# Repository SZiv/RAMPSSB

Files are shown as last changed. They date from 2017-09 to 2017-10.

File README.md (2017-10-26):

# RAMPSSB
=== Be sure to take a look at the Wiki before attempting a build: http://reprap.org/wiki/RAMPSSB and if you are curious more as to the development and technological reasoning behind this project, take a look at my blog post at http://scottziv.com/rampssb-bringing-closed-loop-dc-motor-control-to-3d-printers/ ===

RAMPS Servo Board. Released under GPLv3.

Replaces the X and Y stepper drivers on a RAMPS CNC control board with two channel DC motor quadrature encoder control using cheap, common, easy to solder components. Compatable with almost any 0-24V DC motor with a quadrature encoder that uses hall effect, optical, or mechanical rotary encoders. 

Uses a square L298N DC motor driver, attached with standoffs to the PCB, over 2 Arduino Pro Micros for control. PCB board is less than 100m square, so it can be produced for $5 + shipping from Seeedstudio, and the L298N driver board is cheap (like $3), and the controllers, Pro Micros, are maybe 5 bucks a piece.

For more steppers, this is compatable with the Reprap.me stepper expander, or, with some modification, my other board, the RAMPSXB. 

Can also be used as a simple non-RAMPS step/direction to DC encoder motor setup by directly wiring the pins. 

The firmware could use some work, and I am slowly developing it. It does function, but it is not as stable as I would like. If anyone has better luck with control software, let me know and I can add it to the official repo.

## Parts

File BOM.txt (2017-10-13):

1x PCB
1x L298N DC motor driver (the square kind)
2x Arduino Pro Micro (NOT PRO MINI! Sparkfun makes these, but there are plenty of clones) 
1x filtering capacitor for the motor power if you think its nessissary.
a bunch of male and female pin headers
3x M3x20mm spacers w/screws and nuts
1x M3x5 screws with nuts
1x 3D printed "RAMPSSBSingleFanMount.stl"
1x 40mm fan

If you are dealing with a lot of power, the drivers are stackable, and two pins are included for each control pin, so you dont need to splice wires for two drivers. However, you can theoretically stack these as high as you want and run them in parallel. Drivers can handle about 2 amps per channel.
1x L298N DC motor driver (the square kind)

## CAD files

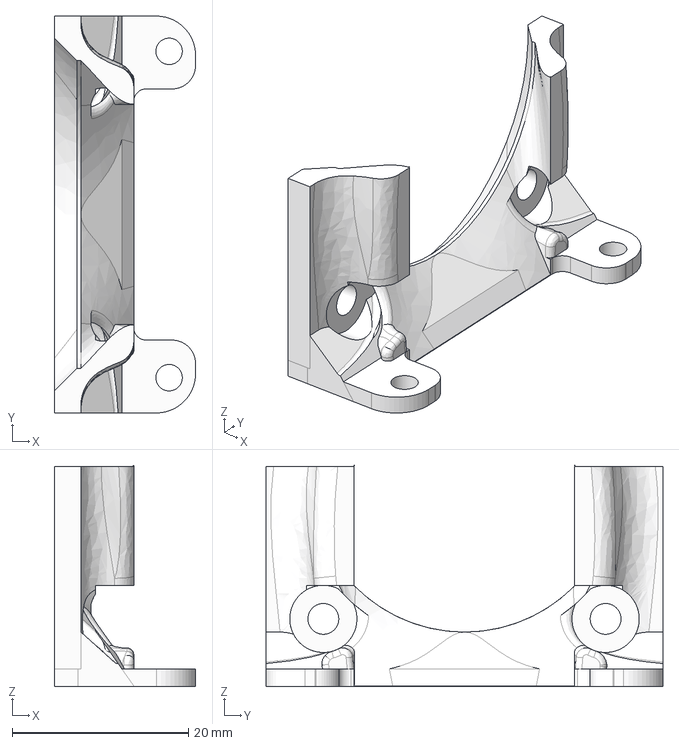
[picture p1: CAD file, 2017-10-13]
Models/RAMPSSBSingleFanMount.step
16.0 x 45.0 x 25.1 mm

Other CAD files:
Models/RAMPSSBSingleFanMount.stl

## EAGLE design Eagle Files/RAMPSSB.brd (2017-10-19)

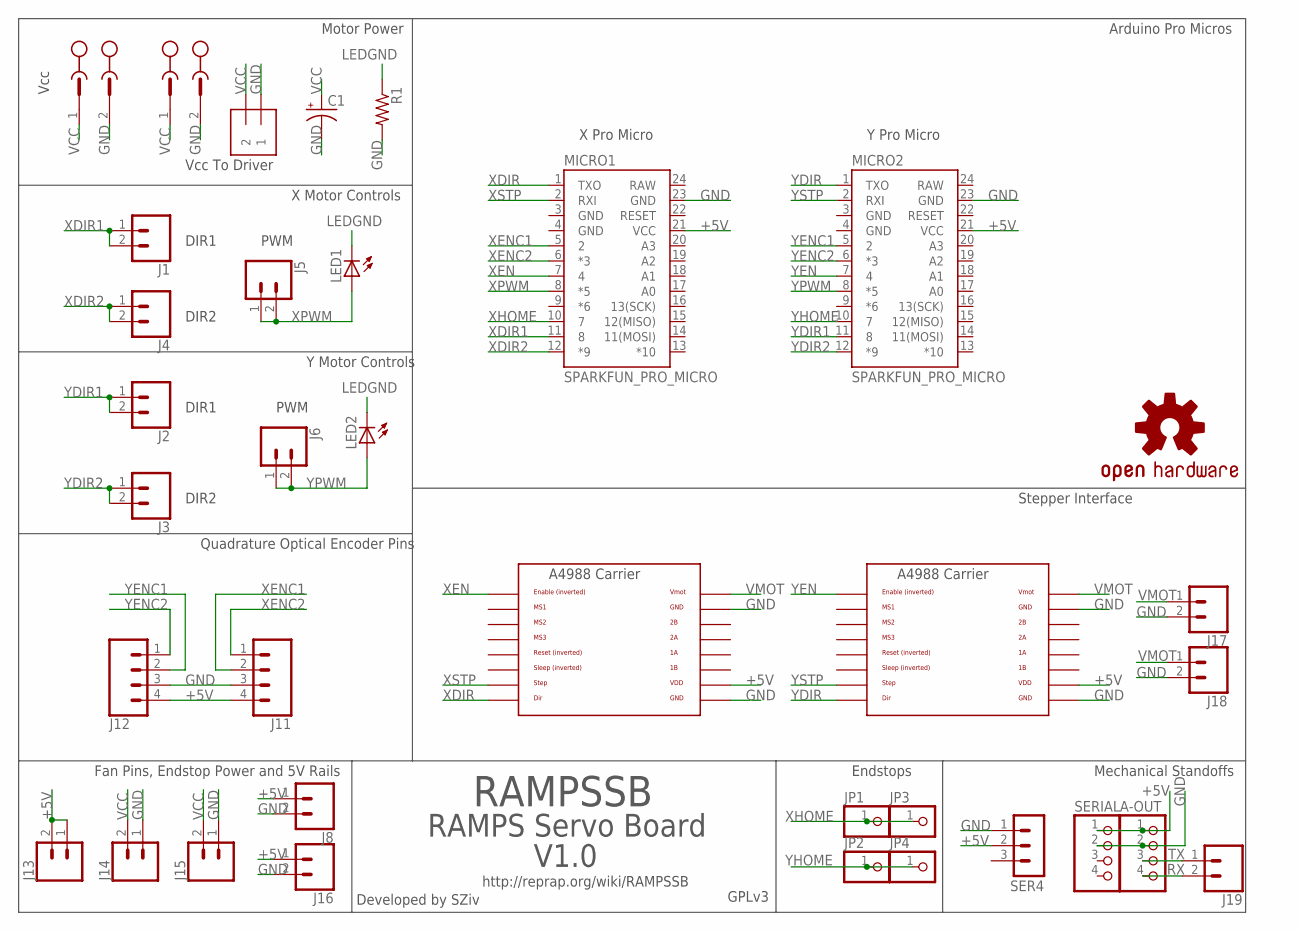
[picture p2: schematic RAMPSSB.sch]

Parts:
A-OUT: PINHD-1X4; 1X04
C1: CPOL-USE2.5-6; E2,5-6
J1, J2, J3, J4, J5, J6, J8, J13, J14, J15, J16, J17, J18, J19: CONN_02; 1X02
J7, J9: OSTTH020160; EDSTL130-02
J10: 1X2-3.5MM
J11, J12: CONN_04; 1X04
JP1, JP2, JP3, JP4: PINHD-1X1; 1X01
LED1, LED2: LED3MM
LOGO1: OSHW-LOGOL; OSHW-LOGO-L
MICRO1, MICRO2: SPARKFUN_PRO_MICRO
R1: R-US_0207/7; 0207/7
SER4: 3PIN-HEADER
SERIAL: PINHD-1X4; 1X04
U$6, U$7: A4988BREAKOUT

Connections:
+5V: A-OUT.1, J8.1, J11.4, J12.4, J13.1, J13.2, J16.1, MICRO1.21 (VCC), MICRO2.21 (VCC), SER4.2, SERIAL.1, U$6.VDD, U$7.VDD
GND: A-OUT.2, C1.-, J7.2, J8.2, J9.2, J10.1, J11.3, J12.3, J14.1, J15.1, J16.2, J17.2, J18.2, MICRO1.3 (GND), MICRO1.4 (GND), MICRO1.23 (GND), MICRO2.3 (GND), MICRO2.4 (GND), MICRO2.23 (GND), R1.2, SER4.1, SERIAL.2, U$6.GND, U$6.GND@0 (GND), U$7.GND, U$7.GND@0 (GND)
LEDGND: LED1.K (C), LED2.K (C), R1.1
RAW: MICRO1.24 (RAW), MICRO2.24 (RAW)
RX: A-OUT.4, J19.2
TX: A-OUT.3, J19.1
VCC: C1.+, J7.1, J9.1, J10.2, J14.2, J15.2
VMOT: J17.1, J18.1, U$6.VMOT, U$7.VMOT
XDIR: MICRO1.1 (TXO), U$6.DIR
XDIR1: J1.1, J1.2, MICRO1.11 (8)
XDIR2: J4.1, J4.2, MICRO1.12 (*9)
XEN: MICRO1.7 (4), U$6.EN
XENC1: J11.2, MICRO1.5 (2)
XENC2: J11.1, MICRO1.6 (*3)
XHOME: JP1.1, JP3.1, MICRO1.10 (7)
XPWM: J5.1, J5.2, LED1.A, MICRO1.8 (*5)
XSTP: MICRO1.2 (RXI), U$6.STEP
YDIR: MICRO2.1 (TXO), U$7.DIR
YDIR1: J2.1, J2.2, MICRO2.11 (8)
YDIR2: J3.1, J3.2, MICRO2.12 (*9)
YEN: MICRO2.7 (4), U$7.EN
YENC1: J12.2, MICRO2.5 (2)
YENC2: J12.1, MICRO2.6 (*3)
YHOME: JP2.1, JP4.1, MICRO2.10 (7)
YPWM: J6.1, J6.2, LED2.A, MICRO2.8 (*5)
YSTP: MICRO2.2 (RXI), U$7.STEP

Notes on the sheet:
DIR1
DIR2
PWM
Vcc To Driver
Vcc
Motor Power
X Motor Controls
Y Motor Controls
Quadrature Optical Encoder Pins
Fan Pins, Endstop Power and 5V Rails
Mechanical Standoffs
Stepper Interface
Arduino Pro Micros
RAMPSSB
RAMPS Servo Board
V1.0
Developed by SZiv
GPLv3
http://reprap.org/wiki/RAMPSSB
Endstops
X Pro Micro
Y Pro Micro

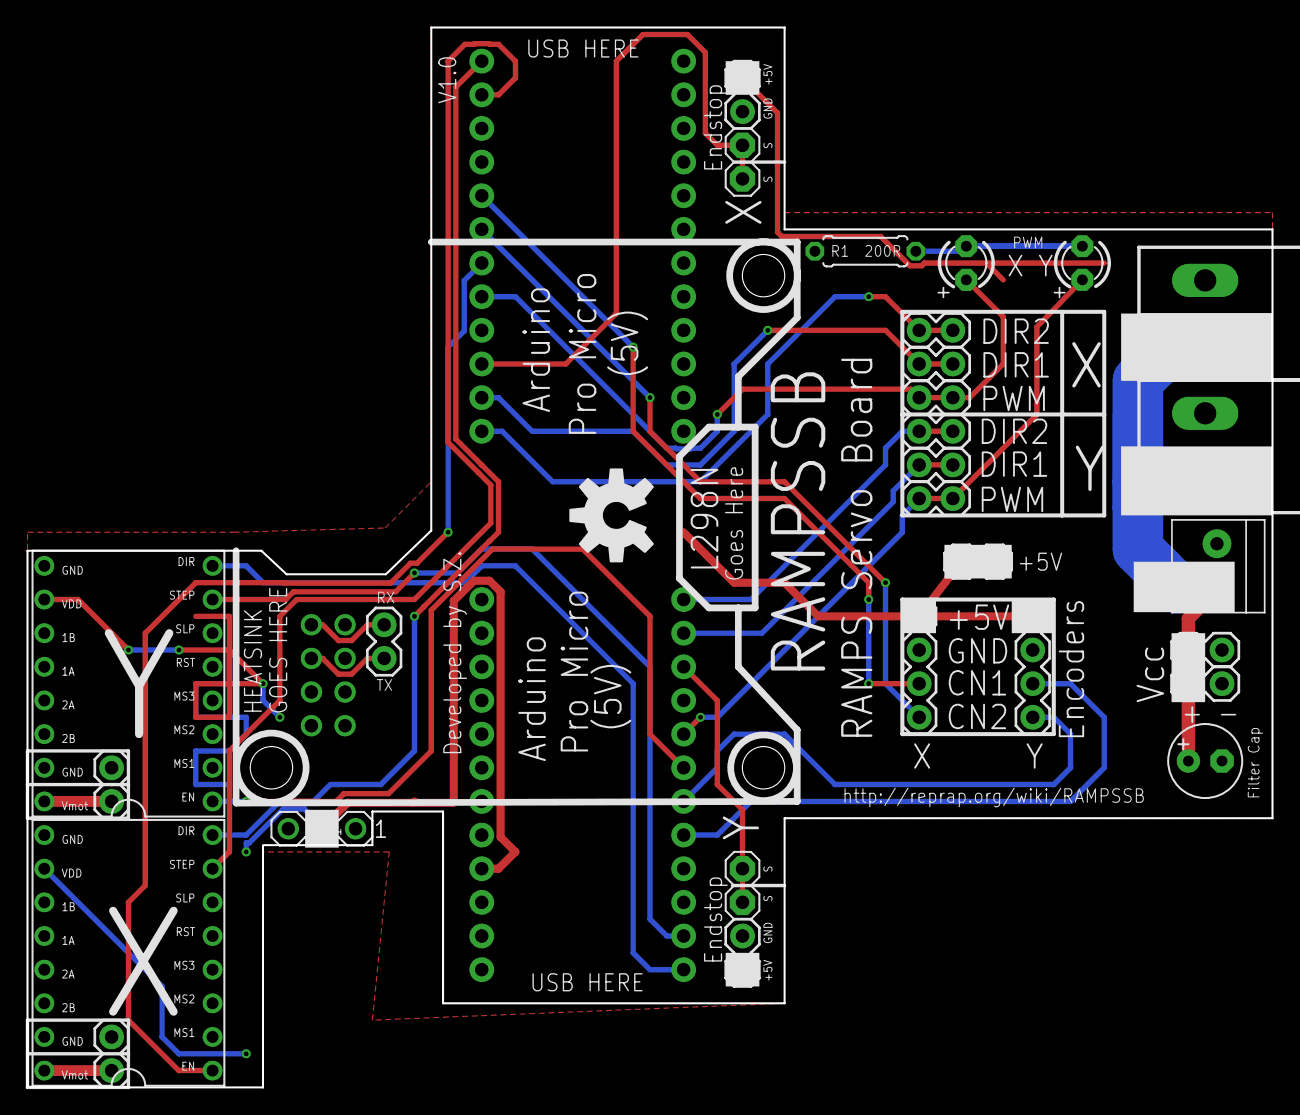
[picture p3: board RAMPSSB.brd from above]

Board: 2 copper layers, 94.0 x 80.0 mm, 35 parts (0 on the bottom side), 26 nets.

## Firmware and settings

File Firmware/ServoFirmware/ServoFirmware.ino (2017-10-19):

#include <Encoder.h> //include encoder library
#include <PID_v1.h> //include PID library
#include "GPIO.h" //include GPIO library

// RAMPSSB Firmware
// Developed by SZiv, released under GPLv3
// Uses PJRC's Encoder library, mikaelpatel's Arduino-GPIO library, as well as Brett Beauregard's PID library. Kudos to them for their hard work!
// Be sure to check out http://reprap.org/wiki/RAMPSSB for more information.

//if you have a better idea of control systems than I, please let me know so I can update the firmware on the official github. It does work, but it has some wobbling error.

//Configuration variables 

//Change these values for your hardware!
#define quadrature true //Is this a quadrature encoder? If so, make true. If you are using a single encoder motor, you will lose a lot of accuracy, but make true (Coming soon!).  
#define cpr 2000.0 //How many counts per revolution? This should be written on the motor datasheet, but its best to test it anyway, because sometimes quadrature encoders have 4 times the noted ticks, because each quadrature counts as 4.
#define mmpr 10 //Millimeters per revolution. This is the DC motor version of "steps per mm" and varies with hardware and gearing. this is easy to test by marking your carriage, rotating the encoder shaft 1 full revolution and measure the distance the carriage moved. 
#define steps_per_mm 80 //What are the steps per mm that the firmware on the RAMPS is using?
#define kp 10 //Proportional Constant. Used for PID control. Tune this to your hardware to get better accuracy. 
#define ki 0 //Integral Constant. Used for PID control. Tune this to your hardware to get better accuracy.
#define kd 1 //Derivative Constant. Used for PID control. Tune this to your hardware to get better accuracy.
#define diagnostic true //If true, sets machine to diagnostic. Prints out location values over serial and can do PID autotuning. Causes a heart attack and bad location data if kept on, so uses it to get PID values and then turn it off.
#define endstopinverted false //By default, endstops are NO. If you are using an NC endstop (like an optical one), change to true.
#define maxpwm 255 //Max PWM you can use on the motor and still read the encoder. For most small encoders that are 100 counts per rev or so, or the speed is low, you can go up to 255, but if you are using faster motors with higher encoder counts, the arduino may freeze up unless you lower this number.  
#define minpwm 110 //Min PWM you can use to make the motor spin.
#define acceptable_error 0.02 //acceptable error for positioning in mm. so long at the carriage is within this value, it will stop. Lowering this value increases accuracy, but my cause wobbling. 

//end of configuration variables



//Define Pins
#define dir 1
#define stp 0
#define en 4
#define pwmout 5
#define encod1 2
#define encod2 3
#define endstop 7
//direction pin setup
GPIO<BOARD::D8> direction1;
GPIO<BOARD::D9> direction2;

//encoder Setup
Encoder myEnc(encod1, encod2); //declare encoder

//PID Setup
double Setpoint = 0;
double Input;
double Output;
PID pidController(&Input, &Output, &Setpoint, kp, ki, kd, DIRECT); //setup PID Controller

//Global Variables
volatile int direct = 0; //What direction are we going? 0 is towards home, 1 is away
//volatile float target = 0; //What is out target location in mm? Updated with new values every step.
//volatile float current = 0; //where are we now? Reset at home
volatile long ticks = 0; //the number of encoder ticks from home we are.
volatile long counts = 0; //number of encoder ticks we are trying to target.
float error = acceptable_error; //acceptable error in mm of final position.
float CPR = cpr; //turn #define into a float
float MMPR = mmpr; //turn #define into a float
float spmm = steps_per_mm; //turn #define into a float
float target = 0;
float current = 0;

void setup()
{
  pinMode(endstop, INPUT);
  pinMode(stp, INPUT);
  pinMode(dir, INPUT);
  pinMode(en, INPUT);
  pinMode(pwmout, OUTPUT);
  direction1.output();
  direction2.output();
  
  //start diagnostic mode
  if (diagnostic == true)
  {
    Serial.begin(250000);
    Serial.println("Diagnostic Mode is Enabled. Turn this off before running the real thing!");
  }

  //set endstop inturrupts
  if (endstopinverted == false)
  {
    attachInterrupt(digitalPinToInterrupt(endstop), reset, RISING); //Reset when the endstop goes from low to high
  }
  else
  {
    attachInterrupt(digitalPinToInterrupt(endstop), reset, FALLING); //Reset when the endstop goes from high to low
  }

  //set encoder inturrupt
  // attachInterrupt(digitalPinToInterrupt(encod1), incretick, RISING); //Add one more step to the total

  //set step inturrupt
  attachInterrupt(digitalPinToInterrupt(stp), increstep, RISING); //Add one more step to the total
  //set DIR inturrupt
  attachInterrupt(digitalPinToInterrupt(dir), directionchange, CHANGE); //flip direction when

  //turn the PID on
  pidController.SetOutputLimits(minpwm, maxpwm); //constrain PID outputs so that it makes the motor run at all levels
  pidController.SetMode(AUTOMATIC);

  //toggle direction
  toggledirection(); //toggle the direction on the DC motor board.
}

void loop()
{
  ticks = myEnc.read(); //update encoder ticks
  target = counts * (1 / spmm); //this is the location in mm we want to be at. (number of steps from home * Steps/mm)
  current = ticks * MMPR * (1 / CPR); //we are currently at this many mm (Encoder ticks from home * mm per revolution / encoder ticks per revolution)
  Input = abs(target - current) * -1; //Input of the PID is negative of the error
  toggledirection(); //check which direction we are going using the direction pin
  pidController.Compute();   //do the PID computation

  if ((digitalRead(en) == 1)||(abs(Input) < error)) //if the motors are disabled or we are within the error of our target, shut motor off
  {
    analogWrite(pwmout, 0); //shut off motors
  }
  else
  {
    analogWrite(pwmout, Output); //output the PID result
  }

  //print location and diagnostic data
  if (diagnostic == true)
  {
    Serial.print("Target:");
    Serial.print(target);
    Serial.print("mm Actual:");
    Serial.print(current);
    Serial.print("mm Steps:");
    Serial.print(counts);
    Serial.print(" Enc_Ticks:");
    Serial.print(ticks);
    Serial.print(" Error:");
    Serial.print(Input);
    Serial.print(" Direction:");
    Serial.print(direct);
    Serial.print(" PWM:");
    Serial.println(Output);
  }
}

void reset()
{
  //reset supposed an actual position
  myEnc.write(0); //reset our encoder position to 0
  counts = 0; //reset out encoder counts to 0

  //Flip direction to make sure we go forward.
  direction1 = LOW;
  direction2 = HIGH;
}

void increstep()
{
  //add or remove a step from the count
  if (direct == 0) //if we are going backwards
  {
    counts--;
  }
  else
  {
    counts++;
  }
}

void incretick()
{
  //add or remove encoder tick from the count
  if (direct == 0)
  {
    ticks--;
  }
  else
  {
    ticks++;
  }
}


void directionchange()
{
  //check direction and tell the motors
  direct = digitalRead(dir);
  toggledirection();
}

void toggledirection()
{
  //make sure the dc motor is moving in the direction we want it to be
  if (current > target)
  {
    direction2 = LOW;
    direction1 = HIGH;
  }
  else if (current < target)
  {
    direction1 = LOW;
    direction2 = HIGH;  
  }
}

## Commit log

2017-09-23 Main Commit
    First Commit. Still waiting on board to test, and I have yet to write
    the software, but its up here if anyone wants to work with it.
    I havent written the Wiki page yet, but once I get a working version,
    I'll throw it up.
    [RAMPSSB.GBL, RAMPSSB.GBO, RAMPSSB.GBP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]
2017-10-13 Update for publish
    Final update before publish! Get ready!
    Still needs some firmware work, but the hardware is there.
    [RAMPSSB.GBL, RAMPSSB.GBO, RAMPSSB.GBP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]
2017-10-13 Firmware Adjustment
    [RAMPSSB.sch]
2017-10-19 Updated firmware to run Arduino-GPIO to increase speed of digital writes
    [RAMPSSB.brd, RAMPSSB.sch]
2017-10-19 renamed PID_input to Error
    Renamed "PID_Input" to "Error" which is more realistic
    [RAMPSSB.brd, RAMPSSB.sch]

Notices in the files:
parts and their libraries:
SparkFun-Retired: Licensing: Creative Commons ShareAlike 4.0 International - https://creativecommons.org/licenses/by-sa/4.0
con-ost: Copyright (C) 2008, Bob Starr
